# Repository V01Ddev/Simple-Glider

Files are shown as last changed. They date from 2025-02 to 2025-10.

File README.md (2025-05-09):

# Simple-Glider

A ESP 3 channel (only using 2) glider meant to be easy to build.

## Glider
The glider was designed to be a foam and 3d print hybrid. The templates are used to trace nets onto foam board that is then cut out. The fuselage is reinforced using 3d printed cubes. The cockpit is fully 3d printed.

## Transmitter
Using a ESP32 and single Joystick. The transmitter takes the analog input of the joystick and maps it from 0 to 255 for PWM. It will then transmit to the receiver.

## Receiver
Using a ESP8266. The receiver will convert the received value to a PWM output for the servos.

## Building the plane
The 3D printed templates allow for the plan to easily traced on foam board that can then be cut out.

Check out the [build guide](./Glider/BuildGuide.md)

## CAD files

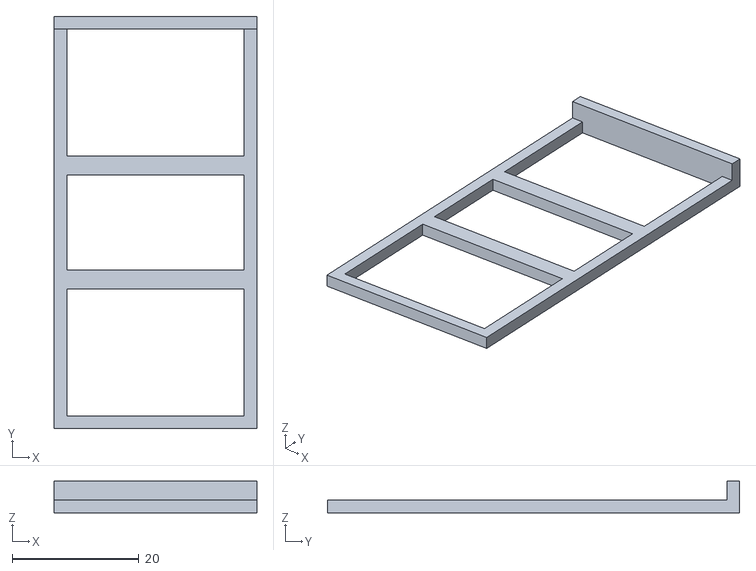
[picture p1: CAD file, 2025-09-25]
Glider/STLs/3mm/FuselageTemplate.stl
32.0 x 65.0 x 5.00

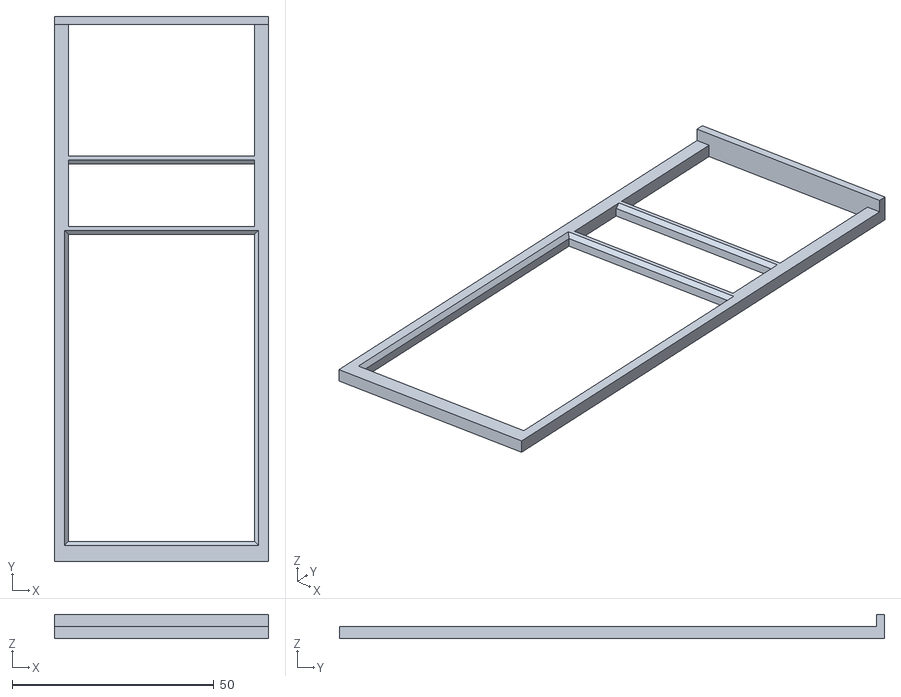
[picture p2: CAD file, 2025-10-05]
Glider/STLs/WingTemplate.stl
53.0 x 135.0 x 6.00

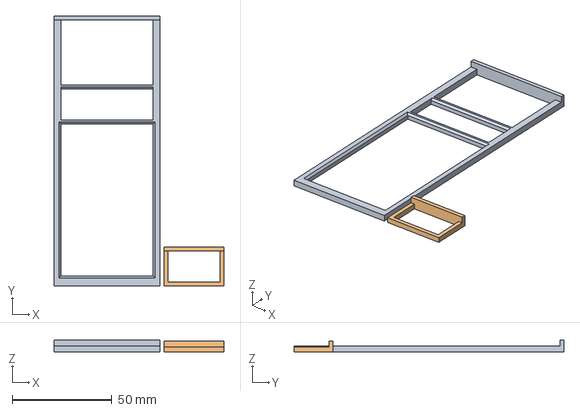
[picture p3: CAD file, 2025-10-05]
Glider/Wing&SparTemplate.FCStd
85.0 x 135.0 x 6.00 mm
WingTemplate
SparTemplate

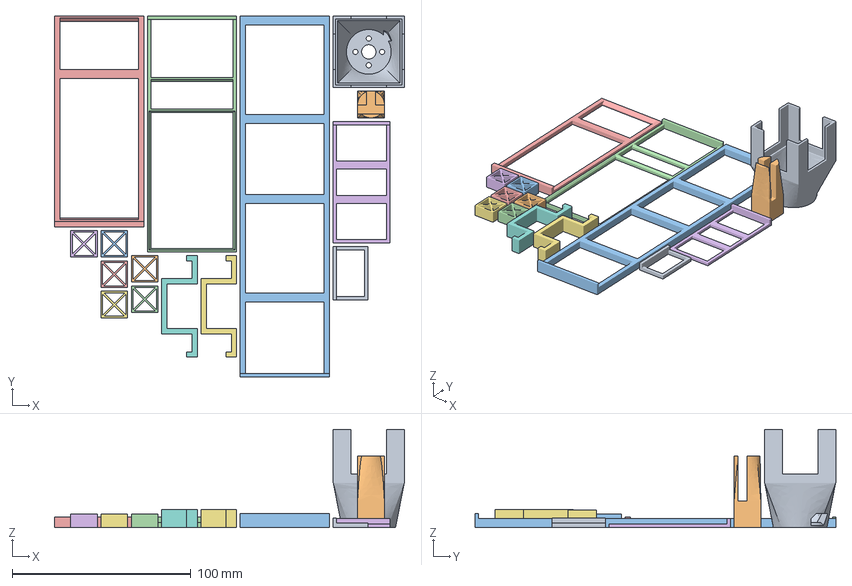
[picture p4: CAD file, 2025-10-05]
SimpleGlider.3mf
196.0 x 202.0 x 55.0 mm
Cockpit.stl
TailFuselageConnector.stl
CockpitTemplate.stl
WingTemplate.stl
StabilizersTemplate.stl
FuselageTemplate.stl
FuselageWingConnector.stl x 2
WingSparTemplate.stl
Reinforcement.stl x 6

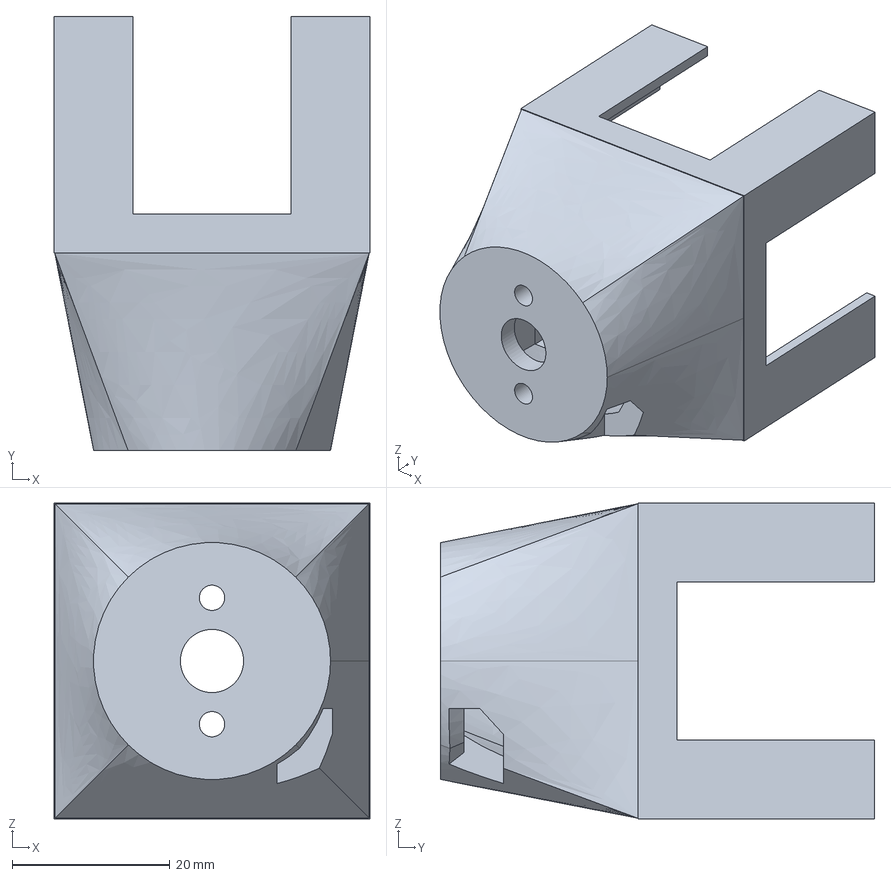
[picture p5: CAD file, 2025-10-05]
Glider/Cockpit.FCStd
40.0 x 55.0 x 40.0 mm

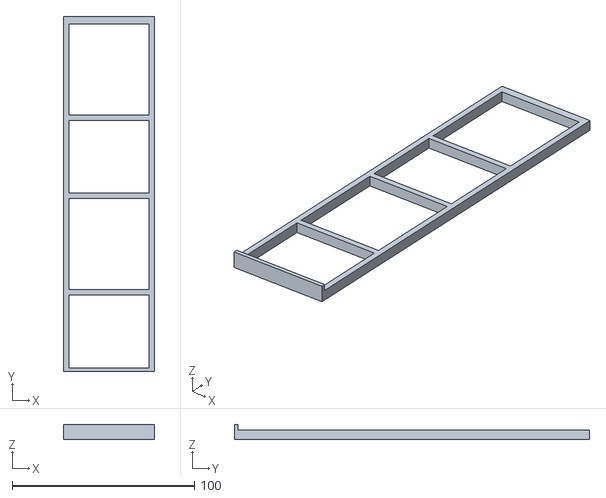
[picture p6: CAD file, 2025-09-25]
Glider/STLs/3mm/CockpitTemplate.stl
50.0 x 195.0 x 8.00

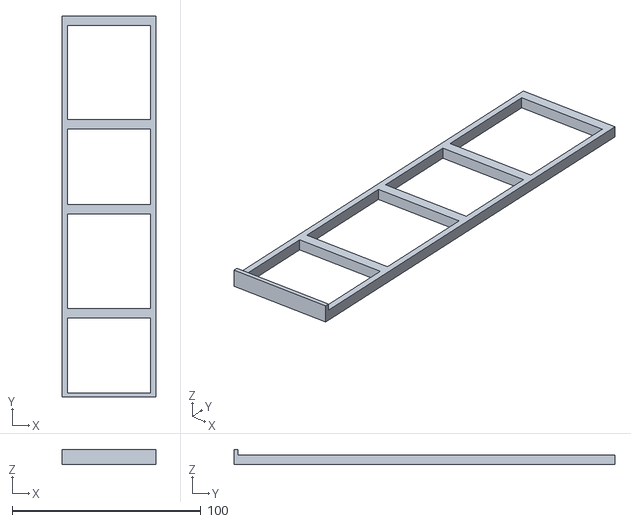
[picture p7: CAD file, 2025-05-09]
Glider/STLs/CockpitTemplate.stl
50.0 x 202.0 x 8.00

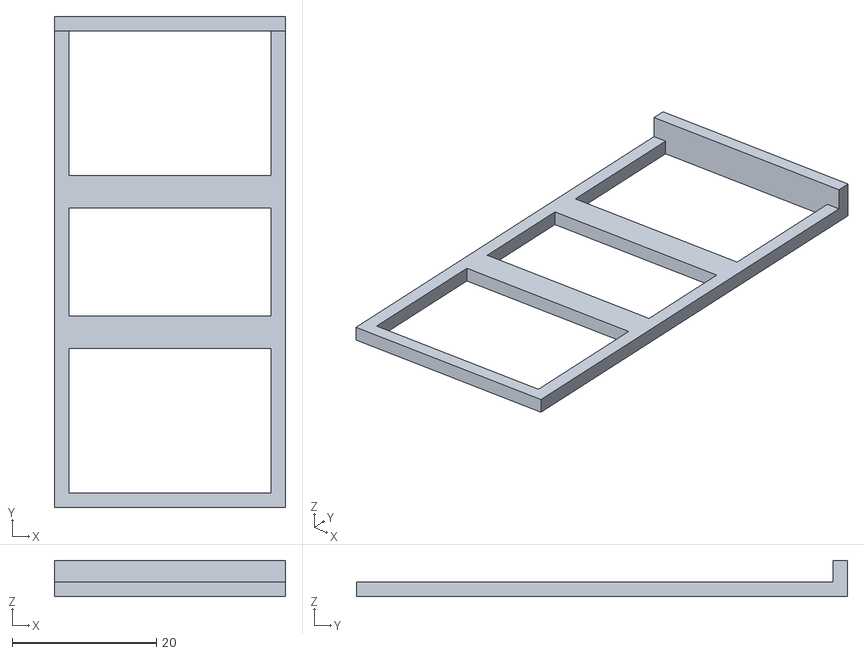
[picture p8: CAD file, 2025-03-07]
Glider/STLs/FuselageTemplate.stl
32.0 x 68.0 x 5.00

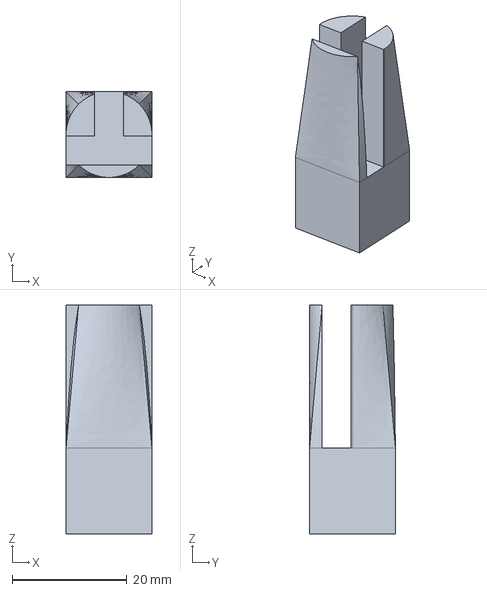
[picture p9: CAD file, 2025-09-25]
Glider/TailFuselageConnector.FCStd
15.0 x 15.0 x 40.0 mm

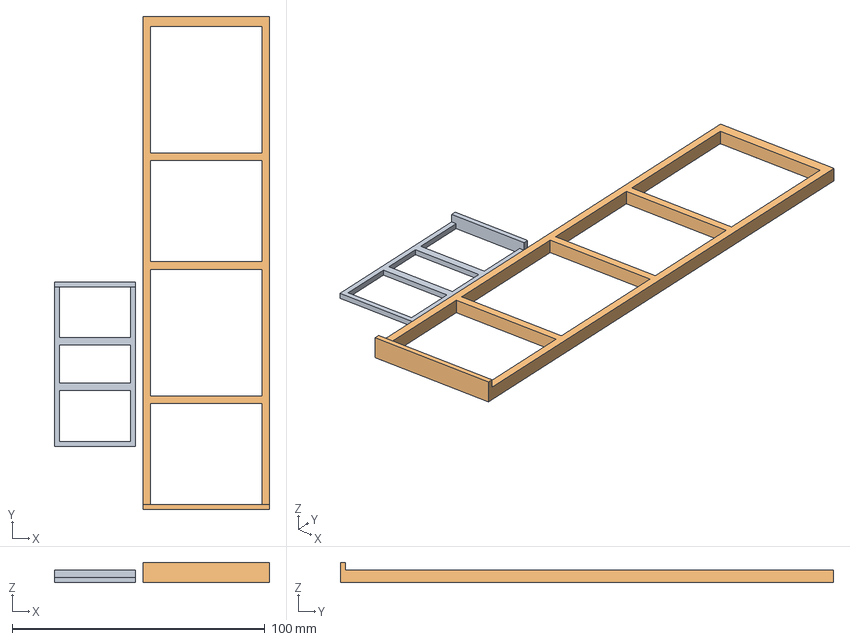
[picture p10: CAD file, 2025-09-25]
Glider/Fuselage&CockpitTemplate 3mm.FCStd
85.0 x 195.0 x 8.00 mm
FuselageTemplate
CockpitTemplate

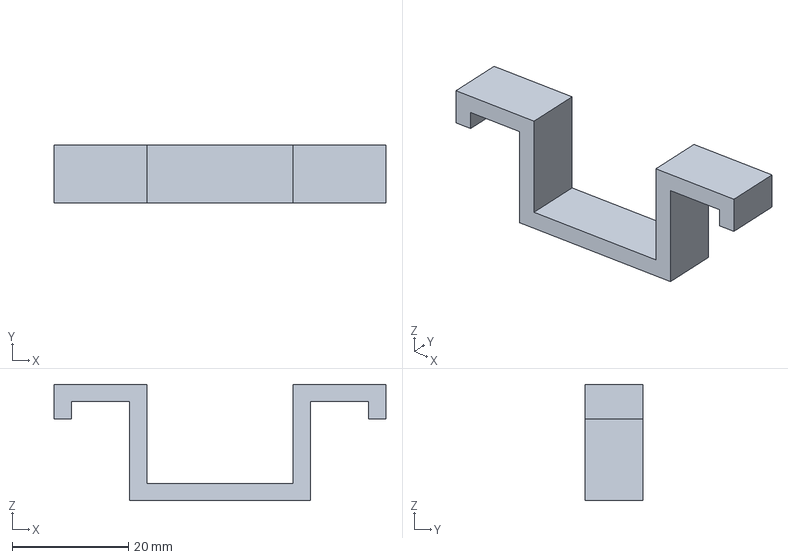
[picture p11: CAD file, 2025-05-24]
Glider/FuselageWingConnector.FCStd
57.0 x 10.0 x 20.0 mm

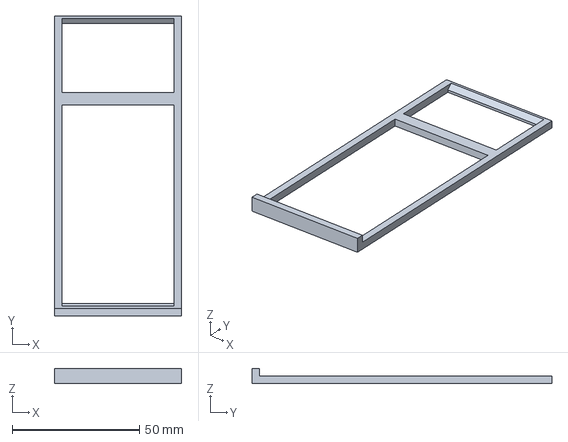
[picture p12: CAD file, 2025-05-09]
Glider/StabilizersTemplate.FCStd
50.0 x 118.0 x 6.00 mm

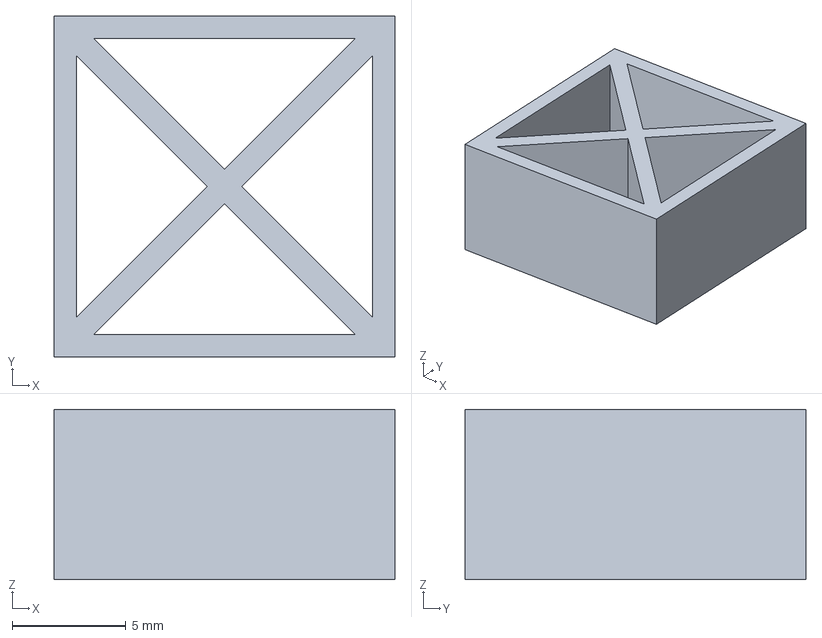
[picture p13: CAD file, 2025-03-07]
Glider/Reinforcement.FCStd
15.0 x 15.0 x 7.50 mm

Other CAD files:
Glider/Fuselage&CockpitTemplate.FCStd
Glider/STLs/Cockpit.stl
Glider/STLs/FuselageWingConnector.stl
Glider/STLs/Reinforcement.stl
Glider/STLs/StabilizersTemplate.stl
Glider/STLs/TailFuselageConnector.stl
Glider/STLs/WingSparTemplate.stl

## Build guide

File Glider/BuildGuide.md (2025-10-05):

# The Simple Plane

This plane is designed to be easily built over a few hours using 3D printed templates.

The lengths of each template component:

```
    Wing Total:         100cm (20cm, 40cm*2)
    Fusalage:           50cm
    Cockpit:            23cm
    Horizontal Stab:    20cm
    Vertical Stab:      16cm
```

You only need to print one of every template piece, any part that that doesn't have `Template` in their name are integrated into the plane. Here is the number of each.

```
    Fusalage Wing Connector:    2
    Reinforcement:              min 8
```
2 of the reinforcement pieces are used to attach the cockpit to the fuselage. The more reinforcement you add to the fuselage the better. 4 pieces has some twist but should be fine for lightweight electronics.

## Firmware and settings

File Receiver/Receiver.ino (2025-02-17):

#include <espnow.h>
#include <ESP8266WiFi.h>
#include <Servo.h>


/*
   pitch    = D5
   roll     = D6
   extra    = D7 undefined for now
 */

# define PPin D5
# define RPin D6


int Roll = 83;
int Pitch = 80;


Servo Pservo; // Pitch
Servo Rservo; // Roll

int PPos = 0; // Pitch PWM output
int RPos = 0; // Roll PWM output


unsigned long now;
unsigned long LastRec;
unsigned long NxtRcv;

// Setting up what the signal would look like
struct Signal {
    byte pitch;
    byte roll;
};

Signal data;


// To run if signal is lost
void DataReset(){
    data.pitch = 90;
    data.roll = 90;
}



void OnDataRecv(uint8_t *mac, uint8_t *incomingData, uint8_t len) {

    memcpy(&data, incomingData, sizeof(Signal));

    Pitch = data.pitch;
    Roll = data.roll;

    LastRec = millis() / 1000;
    NxtRcv = LastRec + 3;

    Serial.print("Pitch: ");
    Serial.println(data.pitch);

    Serial.print("Roll: ");
    Serial.println(data.roll);

    now = millis();
}

void setup(){

    Serial.begin(9600);

    delay(500);

    Pservo.attach(PPin);
    Rservo.attach(RPin);

    DataReset();

    WiFi.mode(WIFI_STA);
    WiFi.disconnect();

    if (esp_now_init() != 0) {
        Serial.println("Error initializing ESP-NOW...");
        return;
    }

    // Sets role
    esp_now_set_self_role(ESP_NOW_ROLE_SLAVE);
    // Does things on callback (when data is sent over)
    esp_now_register_recv_cb(OnDataRecv);
}


int lastRecv = 0;

void loop(){
    now = millis() / 1000;
    if (now > NxtRcv){
        DataReset();
        Serial.println("Connection lost, data has been reset...");
        delay(500);
    }

    PPos = data.pitch;     // pin D5 (PWM signal)
    RPos = data.roll;      // pin D6 (PWM signal)

    Pservo.write(PPos);
    Rservo.write(RPos);
}

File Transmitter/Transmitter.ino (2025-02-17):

#include <SPI.h>
#include "WiFi.h"
#include <esp_now.h>


/*
Right stick:
   X-axis = D32 (pitch)
   Y-axis = D33 (roll)
*/


#define PitchPIN 32
#define RollPIN 33
int Pitch = 0;
int Roll = 0;

// 50:02:91:FF:DB:3A
uint8_t broadcastAddress[] =  {0x50, 0x02, 0x91, 0xFF, 0xDB, 0x3A};
esp_now_peer_info_t peerInfo;

// Setting up what the signal would look like
struct Signal {
    byte pitch;
    byte roll;
};

Signal data;


void setup(){
    Serial.begin(115200);

    pinMode(PitchPIN, INPUT);
    pinMode(RollPIN, INPUT);

    WiFi.mode(WIFI_STA);

    // Initialize ESP-NOW
    if (esp_now_init() != ESP_OK) {
        Serial.println("Error initializing ESP-NOW");
        return;
    }

    // Register the send callback

    // Register peer
    memcpy(peerInfo.peer_addr, broadcastAddress, 6);
    peerInfo.channel = 0; 
    peerInfo.encrypt = false;

    // Add peer        
    if (esp_now_add_peer(&peerInfo) != ESP_OK){
        Serial.println("Failed to add peer");
	return;
    }

    delay(1000);

    Serial.println("Setup complete...");
}



void loop(){
	// map({pin}, {min_value}, {max_value}, 0, 255)

	Roll = analogRead(RollPIN);
	Roll = map(Roll, 0, 4095, 180, 0);

	Pitch = analogRead(PitchPIN);
	Pitch = map(Pitch, 0, 4095, 0, 180);

	// Reversing the pitch
	// Pitch = 255 - Pitch;

	//constrain(Pitch, 45, 135);

	Serial.print("Pitch: ");
	Serial.println(Pitch);

	Serial.print("Roll: ");
	Serial.println(Roll);

	data.pitch = Pitch;
	data.roll = Roll;

	esp_now_send(broadcastAddress, (uint8_t *) &data, sizeof(Signal));

	delay(50);
}

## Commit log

2025-01-25 Initial README + Added all 3d templates and modules
    [FuselageReinforment.FCStd, FuselageReinforment.stl, FuselageTemplate.FCStd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]
2025-01-26 Fixed transmitter code, yet to be tested + Changed receiver pin out comment to the true pin out
    [Receiver.ino, Transmitter.ino]
2025-01-27 Created wing spar template
    [WingSparTemplate.FCStd, WingSparTemplate.stl]
2025-01-27 Started rough work on cockpit
    [Cockpit.FCStd]
2025-02-18 Finished cockpit template
    [Cockpit.FCStd, CockpitTemplate.FCStd, CockpitTemplate.stl]
2025-03-07 Feat: Changed reinforcement to be used to connect cockpit to fuselage
    [Reinforment.FCStd]
2025-03-07 Feat: Changed cockpit template + Build: Re-exported all
    [CockpitTemplate.FCStd, CockpitTemplate.stl, FuselageReinforment.FCStd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]
2025-03-07 Fix: File name spelling mistake
    [Reinforcement.FCStd]
2025-03-07 Fix: fixed file name spelling mistake
    [Reinforcement.stl]
2025-05-09 feat: ease of life pieces, dihedral and stabilizers!
    [Dihedral.FCStd, Dihedral.stl, FuselageWingConnector.FCStd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]
2025-05-09 fix: better looking and easier to build
    [CockpitTemplate.FCStd, CockpitTemplate.stl]
2025-05-19 feat: moving to straight wing, aileron and elevator
    [Dihedral.FCStd, Dihedral.stl]
2025-05-19 feat: one piece for both sides to prevent plastic bullets being launched
    [FuselageWingConnector.FCStd, FuselageWingConnector.stl]
2025-05-24 fix: correct size
    [FuselageWingConnector.FCStd, FuselageWingConnector.stl]
2025-09-05 feat: combined templates and added constants
    [CockpitTemplate.FCStd, Fuselage&CockpitTemplate.FCStd, FuselageTemplate.FCStd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]
2025-09-25 fix: better combined design
    [Fuselage&CockpitTemplate.FCStd]
2025-09-25 feat: 3mm foam support
    [CockpitTemplate.stl, Fuselage&CockpitTemplate 3mm.FCStd, FuselageTemplate.stl]
2025-09-25 feat: 3d printed cockpit, foam and PLA hybrid
    [Cockpit.FCStd, Cockpit.stl]
2025-09-25 feat: tail to fuselage connection
    [TailFuselageConnector.FCStd, TailFuselageConnector.stl]
2025-10-05 feat: working motor mount
    [Cockpit.FCStd, Cockpit.stl]
2025-10-05 chore: updated cockpit
    [SimpleGlider.3mf]
2025-10-05 feat: thicker wing template
    [Wing&SparTemplate.FCStd, WingTemplate.stl]
2025-10-05 fix: correct fuselage length, I think...
